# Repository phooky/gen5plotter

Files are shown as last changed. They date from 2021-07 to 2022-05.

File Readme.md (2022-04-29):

# g5plot

This software will allow you to control a generation 5 Makerbot Replicator and adapt it as a plotter.
It's adapted to my particular circumstances; ymmv. This is mostly to help myself remember when I come 
back to this project or find another junked G5.

## Initial setup

0. Disassemble the replicator until you have access to the main "birdwing" board.

1. Find the J5 connector on the birdwing board, right next to the speaker. The silkscreen will include the 
label "USB2TTL" and therevwill be an arrow pointing to Pin 1.  This is a 3.3V level serial console interface using a standard FTDI cable pinout. You can find a 3.3V FTDI USB-to-serial cable, or program an arduino or similar board with 3.3V I/O levels to act as a bridge. See the pinout section for details.

2. Open up your serial port in `tio`, `minicom`, or some other simple console. Be sure to set your baud rate to 115200. Next, turn on the PSU and push the "PowerOn" button on the birdwing board. After a few moments, you should see boot messages scrolling by. Eventually you will see a login prompt. Log in as "root"; no password should be necessary.

3. Remount the root partition as read/write: `mount -o remount,rw /`

4. Change the hostname. For convenience, I've named mine 'gen5'. If you use something else you'll need to edit the hostname in the Makefile if you want the 'deploy' and other remote targets to work. You can change the hostname by editing the `/etc/hostname` file and rebooting (or in theory running the 'hostname' utility).

5. Plug in the wired ethernet, or set up the wifi. I'm not going to document the wifi configuration here, but you can probably set it up with the 'nmcli' utility.

5. Add your public key to the /var/ssh/authorized_keys file. Run "/etc/init.d/S50sshd restart".

6. Stop the 'kaiten' process. Remove the 'kaiten' from the /etc/init.d directory (or better yet move it somewhere safe) to stop it from launching on boot. Reboot.

## Building and installing g5plot

1. Install cross-platform toolchain for ARM Linux (arm-linux-gnueabi-gcc).

2. Build PASM and the app loader libraries with the "build_tools.sh" script.

3. #`(cd g5plot && make)`

## Deploying and running

You can deploy g5plot by running `make deploy` from the g5plot directory. It relies on the hostname being `gen5`; you can either change the default in the Makefile or set the `PLOTTER` environment variable to the plotter's name.

By default g5plot is deployed to `/var/scratch/g5plot`. If you want to deploy it outside of the `/var` tree you'll need to remount the root partition as read/write.

You can use the `g5p_start.sh` and `g5p_stop.sh` scripts to start and stop the plotter process. Commands should be piped to `/var/run/plotter`.

## TODOs

* Start using the speaker for alerts

## Pinouts

### J5 UART

To connect to the birdwing board you will need to wire up GND, TX, and RX only. It's safest to leave the other pins disconnected.

| Pin | Function |
|-----|---|
|  1  | GND |
|  2  | CTS (ignore) |
|  3  | VCC (ignore) |
|  4  | TX |
|  5  | RX |
|  6  | RTS (ignore) |

### Servo hookup

TODO

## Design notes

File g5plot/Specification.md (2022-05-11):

== Overview

The plotter is controlled by the `g5plot` process, which takes simpled
commands from standard input and uses them to control the plotter. It
terminates and shuts down the plotter cleanly when it receives a SIGINT
signal. SIGSTOP/SIGTSTP and SIGCONT can be use to pause and continue
execution, but be aware that the currently queued commands will
continue to be executed if SIGSTOP is sent. SIGTSTP will immediately
halt the PRUs and reenable them on continuation.

== Interface

=== g5plot interface

Commands are seperated by newlines. All parameters are floats if not
otherwise specified.

| command code | parameters | explanation |
|---|---|---|
| U | - | toolhead up (to preset value) |
| D | - | toolhead down (to preset value) |
| M | X Y V | move toolhead. X and Y are in mm, V is in mm/sec. |
| R | X Y V | move toolhead relative to last position. X and Y are in mm, V is in mm/sec. |
| T | V | move toolhead to velue. Toolhead value is a one-byte unsigned integer. |
| Z | - | set current position as zero/home. |
| O | - | all steppers off |
| H | - | home toolhead to 0,0. |
| Q | - | shut down plotter. |
| W | - | wait for user intervention (NOT YET IMPLEMENTED) |

While g5plot can be driven directly from the command line, the
intended use is to have it receive commands from a fifo, generally
`/var/run/plotter`.

=== Plotter queue management

* dropping and launching prepared files
* modules for handling gcode and svg
* simulator

== Internals

Command queue is in PRU0 data RAM, which is 0x1ff bytes long.
A command is five 32-bit words (16 bytes): a velocity for each axis,
a total length in PRU ticks, and four bytes for axis direciton/enable
and top-level commands.

We do not use interrupts; instead we busy-wait on a ready bit in each
command. That means that to reliably perform a command, it needs to be
written twice: once without the ready bit set, and again with it set.

It's possible that this is unnecessary, as we could put the flag in 
the last byte to be written, but it's not worth the effort to find out
for a useless optimization.

=== Command Queue

The command queue is 20 commands long. The command queue
offset should is reset manually by the sender. Ordinarily it
resets it after 18 commands, but this could be changed easily.

=== Command byte

The command byte is a bitfield. Every command is a "move toolhead"
command, so if the command is only for the toolhead or is a dwell, the
[xyz]_period fields should be set to 0xffffffff.

The bits on the command flag are:

| bit | name | explanation |
|-----|---|---|
| 0 | WAIT | 'WAIT' is deprecated. |
| 1 | READY | The READY flag is set when a command is ready to be executed, and cleared by the PRU once execution has started. |
| 2 | RESET | After this command is executed, the PRU should begin reading the next command from the start of the command buffer. |
| 3 | TOOLHEAD | This command contains a toolhead payload byte which should be sent to the toolhead PRU. |

== TODO

What about acceleration?

What about zeroing?

At start of command, we have a current X Y Z

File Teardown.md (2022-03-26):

# Controlling a Gen 5 Replicator

## Introduction and motivation

A while back I was gifted a busted-up Makerbot Replicator Generation 5 (henceforth just "gen5"). It
was too mechanically damaged to serve as a printer again, but I figured I could pull out the gantry 
and use it as a pen plotter. Unfortunately the existing software on the gen5 was unsuitable for
my purposes, and I ended up having to write a new stepper driver from scratch.

## Anatomy

This is a quick breakdown of the major parts of the gen5. This is all based on my teardown, comments
in the software, and silkscreens on the PCBs; Makerbot may use other terminology.

* Birdwing - the mainboard. Carries the AM1808 processor and the X/Y/Z stepper drivers, along with
    ethernet, wifi, and a six-pin serial console connection.
* Hoboken - the interface PCB. Hoboken includes the knob and buttons, the screen, the thumbdrive USB port,
    the camera, and the chamber lighting LED. Hoboken is connected to Birdwing via an HDMI cable and standard
    connectors. The cable does not actually carry HDMI signals. The video is routed over a single
    signal pair. There is a USB hub on board that routes signals from the camera and thumbdrive.
* Bronx - the toolhead PCB. This is the PCB inside the toolhead, not the one inside the extruder. It has a
    stepper driver and probably some mosfets. It connect via a large flexible flat cable.
* PSU - a small ATX power supply
* H-bot - the XY gantry is in a so-called "h-bot" configuration, with one continuous belt.

## Getting in

### Step one: console

Find the J5 connector on the birdwing board, right next to the speaker. The silkscreen will include the 
label "USB2TTL" and there
will be an arrow pointing to Pin 1.  This is a 3.3V level serial console interface using a standard FTDI cable
pinout. You can find a 3.3V FTDI USB-to-serial cable, or program an arduino or similar board with 3.3V I/O levels
to act as a bridge.

Open up your serial port in `tio`, `minicom`, or some other simple console. Be sure to set your baud rate to 115200.
Next, turn on the PSU and push the "PowerOn" button on the birdwing board. After a few moments, you should see boot
messages scrolling by. Eventually you will see a login prompt. Log in as "root"; no password should be necessary.

### Step two: ethernet and ssh

add pub key to /var/ssh/authorized_keys 
`# /etc/init.d/S50sshd restart`

### Step three: stop kaiten

## Build instructions

build pasm
get arm tools
build entire thing

The easiest way is to use a 115200
 
I'll just refer to the Replicator as the "gen5" going forward.

## TODOs

* Where is the speaker?

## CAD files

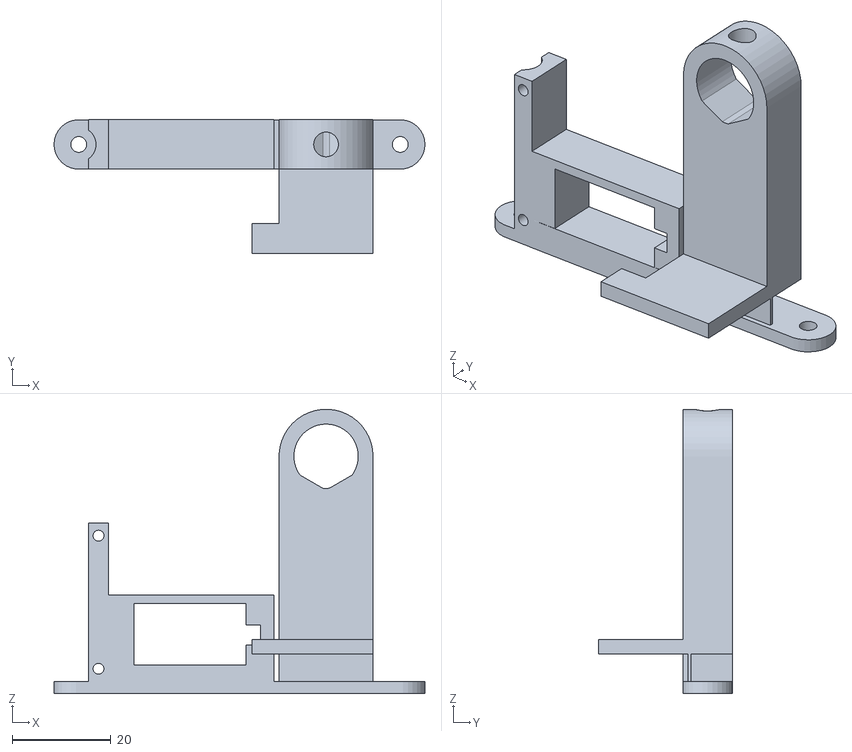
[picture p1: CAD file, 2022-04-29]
hardware/penholder.stl
75.0 x 27.0 x 57.5

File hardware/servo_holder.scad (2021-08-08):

m3_head_clearance = 5.3;
m3_screw_clearance = 3.2;
$fn=30;

module m3_bolt(bolt_len) {
    head_len=5;
    translate([0,0,bolt_len/2]) cylinder(d=m3_screw_clearance,h=bolt_len+0.05,center=true);
    translate([0,0,-head_len/2]) cylinder(d=m3_head_clearance,h=head_len,center=true);
}

module bolts(hole_distance,bolt_len) {
    translate([hole_distance/2,0,0]) m3_bolt(bolt_len);
    translate([-hole_distance/2,0,0]) m3_bolt(bolt_len);
}

// clearance between bolthole center and belt
upper_clearance = 5.0;

// measured parameters
hole_distance = 65.0;
bolt_len = 15.0;

module support(support_th) {
    difference() {
        hull() {
            translate([hole_distance/2,0,support_th/2])
                cylinder(r=upper_clearance,h=support_th,center=true);
            translate([-hole_distance/2,0,support_th/2])
                cylinder(r=upper_clearance,h=support_th,center=true);
        }
        translate([0,0,-0.05]) bolts(hole_distance, bolt_len);
    }
}

servo_screw_hole_d = 1.8;

module pillar() {
    ht_to_under_flange=16;
    difference() {
        hull() {
            translate([0,0,2.5]) cube([4.5,upper_clearance*2,5],center=true);
            translate([0,0,ht_to_under_flange-2.5]) cube([4.5,12,5],center=true);
        }
        translate([1,0,ht_to_under_flange]) cylinder(d=servo_screw_hole_d,h=16,center=true);
    }
}

module pillars() {
    translate([27.5,0,0]) pillar();
    difference() {
        mirror([1,0,0]) pillar();
        translate([0,2.7,0]) cube([10,10,12],center=true);
    }
}

support(2.5);
translate([-15,0,0]) {
color([1,0,0])
#translate([-1.5,-50-(12-upper_clearance*2)/2,16 + 2.5]) import("sg90.stl",convexity=3);
translate([0,0,2.49]) pillars();
}
//translate([0,0,2.49])
//hinge_a();
//rotate(-90,[1,0,0])
//translate([0,-2.9,0]) simple_penholder(15);

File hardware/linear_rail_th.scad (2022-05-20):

use <sg90.scad>
use <mounting.scad>

// Constants

// ----- M2 fastener -----
m2_bolt_head_dia = 3.8; // mm
m2_bolt_head_clearance_dia = 4.4; // mm
m2_bolt_head_height = 2; // mm
m2_bolt_thread_dia = 2; // mm
m2_bolt_thread_clearance_dia = 2.4; // mm
m2_bolt_length = 10; // mm

// ----- Linear rail -----
rail_width = 9; // mm
rail_height = 6.3; // mm
rail_length = 100; // mm
m2_mounting_height = 4.6; // mm
rail_first_hole_offset = 10; // mm
rail_successive_offset = 20; // mm

// ----- M2 hex nut ------
m2_hex_width = 4; // mm
m2_hex_nut_depth = 1.6; // mm (usual depth)
m2_hex_width_clearance = 4.5; // mm

// ----- Linear rail support -----
rail_support_height =  m2_bolt_length - m2_mounting_height; // mm
// support has a lip at one end to help locate the rail vertically
rail_support_lip_width = 1.5; // mm
rail_support_lip_height = 1; // mm

module m2_fastener_hole(length = 20, head_ht = 20) {
    $fn = 40;
    // The hole is located with the origin at the base of the head.
    // The fastener is oriented with the thread in the -Z direction.
    cylinder(d=m2_bolt_head_clearance_dia, h=head_ht); // bolt head
    // threaded bolt
    translate([0,0,-length])
	cylinder(d=m2_bolt_thread_clearance_dia, h=length+0.1); // 0.1 adjustment to ensure overlap
}

// mock fastener for assembly testing
module m2_fastener(length = m2_bolt_length, head_ht = 2) {
    $fn = 40;
    // The hole is located with the origin at the base of the head.
    // The fastener is oriented with the thread in the -Z direction.
    cylinder(d=m2_bolt_head_dia, h=head_ht); // bolt head
    // threaded bolt
    translate([0,0,-length])
	cylinder(d=m2_bolt_thread_dia, h=length+0.1); // 0.1 adjustment to ensure overlap
}

module rail_holes(rail_length = 100, mocks=false) {
    // located from bottom center of one end of the rail; rail extends in +Y direction
    for (offset = [rail_first_hole_offset : rail_successive_offset : rail_length]) {
	translate([0,offset,m2_mounting_height])
	    if (mocks) m2_fastener();
	    else m2_fastener_hole();
    }
}

module rail_approximate(rail_length = 100) {
    color("red") difference() {
	translate([-rail_width/2,0,0])
	    cube([rail_width,rail_length,rail_height]);
	rail_holes();
    }
}

module m2_hex_nut_hole(depth=10) {
    // located from the center of the nut, bottom face
    $fn=40;
    intersection_for(theta = [0, 60, 120]) {
	rotate([0,0,theta])
	    translate([0,0,depth/2])
	    cube([m2_hex_width_clearance,100,depth],center=true);
    }
    translate([0,0,-20])
	cylinder(d=m2_bolt_thread_clearance_dia,h=40);
}

module rail_support(rail_length = 100) {
    difference() {
	union() { // rail support + lip
	    translate([-rail_width/2,0,0])
		cube([rail_width + rail_support_lip_width,
		      rail_length,
		      rail_support_height]);
	    translate([rail_width/2,0,rail_support_height])
		cube([rail_support_lip_width,
		      rail_length,
		      rail_support_lip_height]);
	}
	// holes for hex nuts
	for (offset = [rail_first_hole_offset : rail_successive_offset : rail_length]) {
	    translate([0,offset,m2_hex_nut_depth])
		rotate([180,0,0]) m2_hex_nut_hole();

	}
    }
}

//m2_hex_nut_hole();
translate([0,0,rail_support_height]) {
    // #color("green") rail_holes(mocks=true);	
    // #rail_approximate();
}
rail_support();
support(4);

// *** copied from sg90.scad, ugh "use" vs "import" ***
m_body_width = 23;
m_body_wing_height = 2.5;
m_body_depth = 12.5;

// ----- mounting holes ----
sg90_mounting_hole_dia = 2.5; // mm
sg90_mounting_hole_d_from_body = 2.65; // mm
sg90_mounting_hole_separation = m_body_width + sg90_mounting_hole_d_from_body * 2;

module sg90_support() {
    mount_th = 5;
    mount_w = (sg90_mounting_hole_d_from_body*2) - 0.1;
    mount_d = m_body_depth;
    module one_mount() {
	// located with origin at the top of the mounting hole
	difference() {
	    translate([0,0,-mount_th/2])
		cube([mount_w,mount_d,mount_th], center=true);
	    translate([0,0,-mount_th + m2_hex_nut_depth])
		rotate([180,0,0]) m2_hex_nut_hole();
	}
    }
    one_mount();
    translate([sg90_mounting_hole_separation,0,0]) one_mount();
}

sg90_support_height = 10 - m_body_wing_height;
translate([18,30,sg90_support_height]) {
    rotate([0,0,90]) {
	//# sg90_mount_origin();
	sg90_support();
    }
}
// bridge. this is hacky but whatevs, i'm busy
color("orange")
hull() {
    translate([18-m_body_depth/2,27.3,sg90_support_height-5])
	cube([0.05,5.6+sg90_mounting_hole_separation,5]);
    translate([rail_width/2,28,rail_height-5])
	cube([0.05,4+sg90_mounting_hole_separation,5]);
}

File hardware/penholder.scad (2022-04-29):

use <sg90.scad>
use <mounting.scad>

filament_diameter = 1.75 + 0.15;
clip_diameter = 5;
clip_ht = 3.5;

guide_width = 25;
guide_th = 2;

$fn=45;
thumbscrew_bolt_diameter = 5;

clearances_motor = 0.1;
module motor_bracket() {
    cm = clearances_motor;
    difference() {
        translate([-10,0,10])
        cube([34,10,20], center=true);
        translate([-10,18 - (5 + 2.5),12])
        rotate([90,0,0])
        union() {
            minkowski() {
                sg90(horn_angle=30);
                cube([cm,cm,cm], center=true);
            }
            // cable entry clearance
            hull() {
                translate([-0.5,0,12])
                cord(length=3);
                cord(length=4);
            }
        }
    }
}

module pen_holder() {
    ph_h = 10;
    outer_diameter = 19;
    inner_diameter = 13;
    center_to_hinge = 40;
    translate([-outer_diameter/2,0,0])
    cube([outer_diameter,3,27]);
    translate([-15,0,27-6])
    cube([10,3,6]);
    difference() { 
        hull() { // outside of holder
            translate([0,center_to_hinge,0])
            cylinder(h=ph_h,d=outer_diameter);
            translate([-outer_diameter/2,0,0])
            cube([outer_diameter,1,ph_h]);
        }
        translate([0,center_to_hinge,0])
        intersection() {
            cylinder(h=22,d=inner_diameter,center=true);
            translate([0,4.7,0])
            intersection_for( i = [30,-30] ) {
            rotate([0,0,i])
            cube([20,20,22],center=true);
            }
        }
        translate([0,center_to_hinge,ph_h/2])
        rotate([-90,0,0])
        cylinder(d=5, h=20);
    }
}

module pen_hinge() {
    translate([8,-4,0])
    cube([19,0.7,15]);
    translate([8+19/2,5,8])
    rotate([90,0,0])
    pen_holder();
}



gl_ht = 10.0;
gl_width = 32.0;
gl_depth = 4.0;

module guide () {
    difference(){
    translate([-28.5,0,2.5+gl_width/2])
    rotate([0,90,0])
    rotate([90,0,0])
    difference() {
        // body
        cube([gl_width,gl_depth,gl_ht],center=true);
        // filament holes
        for (theta = [90, -90]) {
            rotate([0,0,theta])
            translate([0,(guide_width+filament_diameter)/2,0])
            cylinder(d=filament_diameter+0.3, h=100,center=true);
        }
    }
    translate([-65/2,0,0])
    cylinder(d=7,h=40);
    }
}

//#color("#8080ff") 
//translate([-10,18 - (5 + 2.5),12])
//rotate([90,0,0]) sg90(horn_angle=0);
union() {
    support(2.5);
    motor_bracket();
    guide();
}
color("#00ff00") pen_hinge();

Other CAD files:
hardware/mounting.scad
hardware/sg90.scad
hardware/tap_holder.scad

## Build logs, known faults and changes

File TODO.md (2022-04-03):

* TODO Proper check for whether a command has been executed; we need a bit to indicate that this command has not yet been handled. This will allow us to have proper pipeline stalls, instead of the mess I'm currently grappling with.

* TODO simplify servo PRU design; it should simply run continuously instead of awaiting a signal (with the possible ability to go into "servo off" mode where no pulses are sent)

* DONE QUICK NOTES: not exiting correctly-- hangs on cherchar(), but also wait  for completion. Let's review
  CLOSED: [2022-03-31 Thu 20:01]

* [DONE] find penup/pendown solenoid breakout (gowanus connector?)
* look into homing
* [DONE] check gpio pins:
	DA850_GPIO5_5,	//Chamber heater reserved 0
	DA850_GPIO2_5,	//Chamber heater reserved 1
* [DONE] test basic GPIO toggling from PRU1
* DONE servo test from PRU1
  CLOSED: [2022-03-30 Wed 11:27]
* DONE pru0->pru1 servo command
  CLOSED: [2022-03-30 Wed 11:27]

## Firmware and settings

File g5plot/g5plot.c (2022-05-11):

#include <stdio.h>
#include <stdint.h>
#include <string.h>
#include <stdlib.h>
#include <math.h>
#include <stdbool.h>

// PRU driver headers
#include <prussdrv.h>

#define STEPPER_PRU     0
#define TOOLHEAD_PRU    1

// Command structure that is sent to the PRU.
typedef struct {
    uint32_t x_period;
    uint32_t y_period;
    uint32_t z_period;
    uint32_t end_tick;
    uint8_t direction;
    uint8_t enable;
    uint8_t cmd;
    uint8_t toolhead;
} __attribute__((packed,aligned(4))) Command;

const unsigned int CommandSzInWords = 5;

const unsigned int TH_UP = 30;
const unsigned int TH_DOWN = 200;

// Command byte bit definitions
enum {
    CFL_WAIT = 0,        // Deprecated
    CFL_CMD_READY = 1,   // Indicates that this command is ready for processing.
                         // If this bit is not set, the PRU will busy wait until it is.
    CFL_RST_QUEUE = 2,   // Indicates that after this command is executed, the PRU should go
                         // back to the head of the buffer.
    CFL_TOOLHEAD = 3,    // Indicates that this command is for the toolhead.
};

// A running count of commands processed since g5plot was started.
uint16_t cmds_processed = 0;

// A pointer to the PRU0's data memory, used for command queue management.
uint8_t* prumem = NULL;

// Flag indicating that g5plot is ready to shut down.
static volatile bool shutdown = false;

// Queue management
uint8_t queue_idx = 0; // next empty queue slot
const uint8_t queue_len = 20; // total number of Command entries in queue

// Check if we're running or not
bool is_running = false;

void enqueue(Command* cmd) {
    int byteoff = queue_idx * sizeof(Command);
    volatile Command* prucmd = (Command*)(prumem + byteoff);
    // clear reset flag and ready flag on existing command, just in case
    cmd->cmd &= ~((1 << CFL_RST_QUEUE) | (1 << CFL_CMD_READY));
    // zero the queue after this entry if near the end
    bool zero_queue = (queue_idx >= queue_len - 2);
    if (zero_queue) {
        cmd->cmd |= 1 << CFL_RST_QUEUE;
    }
    // wait for empty command space
    printf("Checking for space at queue entry %d (of %d).\n",
	   queue_idx, queue_len); fflush(stdout);
    if (prucmd->cmd & (1<<CFL_CMD_READY)) {
	uint32_t attempts = 0;
	while ((prucmd->cmd & (1<<CFL_CMD_READY)) && !shutdown) {
	    // pass and busy wait, we should check for timeouts at some point
	    if (attempts == 0xffff) { printf("Busy waiting"); fflush(stdout); }
	    attempts++;
	}
	printf("Block cleared.\n"); fflush(stdout);
    }
    *prucmd = *cmd;
    // Set ready bit
    cmd->cmd |= 1 << CFL_CMD_READY;
    *prucmd = *cmd;
    queue_idx = zero_queue?0:queue_idx+1;
}


/*
 * Machine configuration
 */
const float steps_per_mm = 100.0;
// Maximum X coordinate in millimeters
const float max_x = 252.0;
// Maximum Y coordinate in millimeters
const float max_y = 199.0;
// Maximum velocity in mm/s
const float max_v = 150.0;
// Steps per mm, XY
const float steps_per_mm_xy = 88.573186;
// Steps per mm, Z
const float steps_per_mm_z = 400.0;
// Internal PRU ticks per second (200 MHz)
const float ticks_per_second = 200 * 1000 * 1000;

// Toolhead ticks: needs 0.2s
const uint32_t TH_TICKS = 40L * 1000L * 1000L;

// Homing ticks: needs 5s
const uint32_t HOMING_TICKS = 1000L * 1000L * 1000L;


/*
 * Machine state
 */
// The _machine_ state is maintained as the current position in A and B
// steps. The XY coordinates are always a cache of the XY interpretation
// of the A and B steps.
typedef struct { int32_t a; int32_t b; } AB;
typedef struct { float_t x; float_t y; } XY;
struct {
    AB ab;    // Absolute stepper positions
    XY xy;    // xy coordinates based on ab coordinates
} state = { { 0, 0 }, { 0.0, 0.0 } };

/** Convert XY position or delta to AB position or delta */
AB ab_from_xy(XY xy) {
    int32_t steps_x = (int32_t)(xy.x * steps_per_mm_xy);
    int32_t steps_y = (int32_t)(xy.y * steps_per_mm_xy);
    return (AB){ steps_y + steps_x, steps_y - steps_x };
}

/** Convert AB position or delta to XY position or delta */
XY xy_from_ab(AB ab) {
    int32_t steps_x = (ab.a - ab.b) / 2;
    int32_t steps_y = (ab.a + ab.b) / 2;
    return (XY){ (float)steps_x / steps_per_mm_xy, (float)steps_y / steps_per_mm_xy };
}

/*
 * Enqueue a relative AB move, in steps and timer ticks
 */
void move_rel_ab_time(AB ab, uint32_t ticks) {
    Command cmd;
    cmd.end_tick = ticks;
    cmd.enable = 0x4;
    cmd.direction = 0x1;
    int32_t a = ab.a; int32_t b = ab.b;
    if (a < 0) { cmd.direction ^= 0x1; a = -a; }
    if (b < 0) { cmd.direction ^= 0x2; b = -b; }
    cmd.cmd = 0x00;
    cmd.z_period = ticks + 1;
    //printf("X %d Y %d A %d B %d\n",x_delta,y_delta,a,b);
    cmd.x_period = (a==0)?0x7fffffff:(ticks / (a * 2));
    cmd.y_period = (b==0)?0x7fffffff:(ticks / (b * 2));
    //printf("X_P %d Y_P %d\n",cmd.x_period, cmd.y_period);
    enqueue(&cmd);
    // Update the current machine state
    state.ab.a += ab.a;
    state.ab.b += ab.b;
    state.xy = xy_from_ab(state.ab);
}

/*
 * Home toolhead. This involves just spinning the A axis and disabling the B
 * axis.
 */
void home_toolhead() {
    Command cmd;
    cmd.end_tick = HOMING_TICKS;
    cmd.enable = 0x6;
    cmd.direction = 0x0;
    cmd.cmd = 0x00;
    cmd.y_period = cmd.z_period = 0x7fffffff;
    cmd.x_period = HOMING_TICKS / (max_x * steps_per_mm_xy * 2);
    enqueue(&cmd);
}


/*
 * Disable steppers.
 */
void disable_steppers() {
    Command cmd;
    cmd.end_tick = TH_TICKS;
    cmd.enable = 0x7;
    cmd.direction = 0x0;
    cmd.cmd = 0x00;
    cmd.x_period = cmd.y_period = cmd.z_period = 0x7fffffff;
    enqueue(&cmd);
}

/**
 * Move in XY coordinates relative to the current position.
 * Ignores commands that try to move at exceptionally low speeds.
 * TODO: check for overlong moves (max: 10s)
 * @param dx the delta x coordinate in millimeters (mm).
 * @param dy the delta y coordinate in millimeters (mm).
 * @param v the velocity of the move, in millimeters per second (mm/s).
 */
void move_relative_xy(float dx, float dy, float v) {
    if (fabsf(v) <= 0.1) {
        fprintf(stderr, "Refusing to move at less that 0.1mm/s\n");
        return;
    }
    AB delta = ab_from_xy( (XY){ dx, dy } );
    float len = sqrt(dx*dx + dy*dy);
    uint32_t time_in_ticks = (uint32_t)(ticks_per_second * (len / v));
    move_rel_ab_time(delta,time_in_ticks);
}

/**
 * Move to the specified XY coordinates from current position.
 * @param x the x coordinate in millimeters (mm).
 * @param y the y coordinate in millimeters (mm).
 * @param v the velocity of the move, in millimeters per second (mm/s).
 */
void move_xy(float x, float y, float v) {
    float dx = x - state.xy.x;
    float dy = y - state.xy.y;
    move_relative_xy(dx, dy, v);
}

/**
 * Dwell at given location for a specified time.
 * TODO: check for overlong dwells (max: 10s)
 * @param t the time to dwell, in seconds
 */
void dwell(float time) {
    uint32_t time_in_ticks = (uint32_t)(ticks_per_second * time);
    move_rel_ab_time((AB){0,0},time_in_ticks);
}

void toolhead(int parameter) {
    Command cmd;
    cmd.cmd = 1 << CFL_TOOLHEAD;
    cmd.toolhead = parameter & 0xff;
    cmd.end_tick = TH_TICKS;
    cmd.enable = 0x4;
    cmd.direction = 0x1;
    cmd.z_period = 0x7fffffff;
    cmd.x_period = 0x7fffffff;
    cmd.y_period = 0x7fffffff;
    enqueue(&cmd);
}


/**
 * Set bot's idea of home (0,0).
 */
void set_here_as_home() {
    state.ab = (AB){ 0, 0 };
    state.xy = (XY){ 0.0, 0.0 };
}

/**
 * Enqueue a stop command.
 */
void stop() {
    Command cmd;
    cmd.enable = 0x0;
    cmd.cmd = 1 << CFL_WAIT;
    cmd.end_tick = 200;
    enqueue(&cmd);
}

#include <signal.h>

// Handle SIGINT by setting the shutdown flag.
void handle_sigint(int sig) {
    shutdown = true;
    printf("Interrupted; shutting down.\n");
}

static struct sigaction orig_tstp;

void handle_sigtstp(int sig) {
    prussdrv_pru_pause(0);
    (*orig_tstp.sa_handler)(sig);
}

static struct sigaction orig_cont;

void handle_sigcont(int sig) {
    prussdrv_pru_unpause(0);
    (*orig_cont.sa_handler)(sig);
}

int main(int argc, char** argv) {
    //tpruss_intc_initdata pruss_intc_initdata = interrupt_controller_setup;
    prussdrv_init();	
    if (prussdrv_open(PRU_EVTOUT_0)) { 
        fprintf(stderr, "Could not open uio%d, aborting\n", PRU_EVTOUT_0);
        return -1;
    }
    fprintf(stderr,"Opened PRU.\n");
    
    // Initialize interrupts
    //prussdrv_pruintc_init(&pruss_intc_initdata);

    if (prussdrv_map_prumem(PRUSS0_PRU0_DATARAM, (void**) &prumem) != 0) {
	fprintf(stderr, "Could not map PRU0 data ram! Aborting.\n");
	return -1;
    }
    
    // Clear out command buffer to ensure no accidental commands are run
    {
	const int wordsz = sizeof(Command)*queue_len / 4;
	for (int i = 0; i < wordsz; i++) {
	    *((uint32_t*)prumem + i) = 0;
	}
    }

    // Run PRU programs
    prussdrv_exec_program(TOOLHEAD_PRU, "./servo_pru.bin");
    prussdrv_exec_program(STEPPER_PRU, "./stepper_pru.bin");

    {
	struct sigaction sa_int = { .sa_handler = handle_sigint, .sa_flags = 0 };
	sigaction(SIGINT, &sa_int, NULL);
	struct sigaction sa_tstp = { .sa_handler = handle_sigtstp, .sa_flags = 0 };
	sigaction(SIGTSTP, &sa_tstp, &orig_tstp);
	struct sigaction sa_cont = { .sa_handler = handle_sigcont, .sa_flags = 0 };
	sigaction(SIGCONT, &sa_cont, &orig_cont);
    }

    int cmd;

    while (!shutdown) {
	cmd = getchar();
	if (cmd == EOF) {
	    clearerr(stdin);
	    continue;
	}
	if (cmd == 'U') {
	    printf("Pen up\n");
	    toolhead(TH_UP);
	}
	if (cmd == 'D') {
	    printf("Pen down\n");
	    toolhead(TH_DOWN);
	}
	if (cmd == 'H') {
	    printf("Homing.\n");
	    home_toolhead();
	}
	if (cmd == 'O') {
	    printf("Steppers off.\n");
	    disable_steppers();
	}
	if (cmd == 'Z') {
	    printf("Now at 0,0\n");
	    set_here_as_home();
	}
	if (cmd == 'Q') {
	    printf("Explicit shutdown.\n");
	    shutdown = true;
	}
        if (cmd == 'M') {
            float x_in, y_in, v_in;
            if (scanf("%f %f %f\n",&x_in,&y_in,&v_in) != EOF) {
                move_xy(x_in,y_in,v_in);
                printf("Move to X %f Y %f - V %f\n",x_in,y_in,v_in);
            }
	}
        if (cmd == 'R') {
            float x_in, y_in, v_in;
            if (scanf("%f %f %f\n",&x_in,&y_in,&v_in) != EOF) {
                move_relative_xy(x_in,y_in,v_in);
                printf("Move relative X %f Y %f - V %f\n",x_in,y_in,v_in);
            }
	}
        if (cmd == 'T') {
            int th;
            if (scanf("%d\n",&th) != EOF) {
                toolhead(th);
                printf("Sending %d to toolhead\n",th);
            }
        }
    }

    printf("Out of main loop.\n");

    printf("SUMMARY: oustanding events %d, processed events %d, queue offset %d\n",
	   0, cmds_processed, queue_idx);

    prussdrv_pru_disable(STEPPER_PRU);
    prussdrv_pru_disable(TOOLHEAD_PRU);
    prussdrv_exit ();

    return 0;
}

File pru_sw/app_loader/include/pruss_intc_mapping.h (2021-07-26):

/*
 * pruss_intc_mapping.h
 *
 * Example PRUSS INTC mapping for the application
 *
 * Copyright (C) 2010 Texas Instruments Incorporated - http://www.ti.com/
 *
 *
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
 *    Redistributions of source code must retain the above copyright
 *    notice, this list of conditions and the following disclaimer.
 *
 *    Redistributions in binary form must reproduce the above copyright
 *    notice, this list of conditions and the following disclaimer in the
 *    documentation and/or other materials provided with the
 *    distribution.
 *
 *    Neither the name of Texas Instruments Incorporated nor the names of
 *    its contributors may be used to endorse or promote products derived
 *    from this software without specific prior written permission.
 *
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
*/

/*
 * ============================================================================
 * Copyright (c) Texas Instruments Inc 2010-11
 *
 * Use of this software is controlled by the terms and conditions found in the
 * license agreement under which this software has been supplied or provided.
 * ============================================================================
*/

#ifdef AM33XX
#error ONLY_AM18xx
#define PRU0_PRU1_INTERRUPT     17
#define PRU1_PRU0_INTERRUPT     18
#define PRU0_ARM_INTERRUPT      19
#define PRU1_ARM_INTERRUPT      20
#define ARM_PRU0_INTERRUPT      21
#define ARM_PRU1_INTERRUPT      22
#else
#define PRU0_PRU1_INTERRUPT     32
#define PRU1_PRU0_INTERRUPT     33
#define PRU0_ARM_INTERRUPT      34
#define PRU1_ARM_INTERRUPT      35
#define ARM_PRU0_INTERRUPT      36
#define ARM_PRU1_INTERRUPT      37
#endif
#define CHANNEL0                0
#define CHANNEL1                1
#define CHANNEL2                2
#define CHANNEL3                3
#define CHANNEL4                4
#define CHANNEL5                5
#define CHANNEL6                6
#define CHANNEL7                7
#define CHANNEL8                8
#define CHANNEL9                9

#define PRU0                    0
#define PRU1                    1
#define PRU_EVTOUT0             2
#define PRU_EVTOUT1             3
#define PRU_EVTOUT2             4
#define PRU_EVTOUT3             5
#define PRU_EVTOUT4             6
#define PRU_EVTOUT5             7
#define PRU_EVTOUT6             8
#define PRU_EVTOUT7             9

#define PRU0_HOSTEN_MASK            0x0001
#define PRU1_HOSTEN_MASK            0x0002
#define PRU_EVTOUT0_HOSTEN_MASK     0x0004
#define PRU_EVTOUT1_HOSTEN_MASK     0x0008
#define PRU_EVTOUT2_HOSTEN_MASK     0x0010
#define PRU_EVTOUT3_HOSTEN_MASK     0x0020
#define PRU_EVTOUT4_HOSTEN_MASK     0x0040
#define PRU_EVTOUT5_HOSTEN_MASK     0x0080
#define PRU_EVTOUT6_HOSTEN_MASK     0x0100
#define PRU_EVTOUT7_HOSTEN_MASK     0x0200


#define PRUSS_INTC_INITDATA {   \
{ PRU0_PRU1_INTERRUPT, PRU1_PRU0_INTERRUPT, PRU0_ARM_INTERRUPT, PRU1_ARM_INTERRUPT, ARM_PRU0_INTERRUPT, ARM_PRU1_INTERRUPT,  (char)-1  },  \
{ {PRU0_PRU1_INTERRUPT,CHANNEL1}, {PRU1_PRU0_INTERRUPT, CHANNEL0}, {PRU0_ARM_INTERRUPT,CHANNEL2}, {PRU1_ARM_INTERRUPT, CHANNEL3}, {ARM_PRU0_INTERRUPT, CHANNEL0}, {ARM_PRU1_INTERRUPT, CHANNEL1},  {-1,-1}},  \
 {  {CHANNEL0,PRU0}, {CHANNEL1, PRU1}, {CHANNEL2, PRU_EVTOUT0}, {CHANNEL3, PRU_EVTOUT1}, {-1,-1} },  \
 (PRU0_HOSTEN_MASK | PRU1_HOSTEN_MASK | PRU_EVTOUT0_HOSTEN_MASK | PRU_EVTOUT1_HOSTEN_MASK) /*Enable PRU0, PRU1, PRU_EVTOUT0 */ \
} \

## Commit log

2021-07-07 initial checking of basic stepper engine
2021-07-21 It looks like resetting the cycle counter is... not an actual thing we can do. Looking into using a timer peripheral.
    [stepper_pru.c]
2021-07-23 adding prussdrv library to repo; we're probably going to have to horse around with it to get interrupt stuff working correctly
    [pruss_intc_mapping.h, prussdrv.c]
2021-07-26 switching over to lightly modified version of prussdrv used on the beaglebone, to fix up the mess that is INTC handling
    [pasm.h]
2021-07-27 doing some squares. Problems: - we are skipping the last move in the queue before reset - somehow not getting enough interrupts
    [stepper_pru.c]
2021-07-27 fixing reset queue bit, reducing full queue size
    [stepper_pru.c]
2021-07-28 - fixed too-small offset register size - adding wait-for-start interrupt
    [stepper_pru.c]
2021-07-28 adding commented interface, cleanup, fixing spelling, etc
    [stepper_pru.c]
2021-08-03 initial checkin of toolholder
    [pen_holder.scad]
2021-08-03 starting in on hinge design
    [pen_holder.scad]
2021-08-04 adding a hopefully useful tap handle
    [tap_holder.scad]
2021-08-08 adding another version
    [modular_pen_holder.stl]
2021-08-08 adding servo holder, quick try
    [servo_holder.scad]
2021-08-12 writing PRU code for toggling GPIO manually; this will grow into our servo code
2021-08-13 fixed servo.p PRU address, loading servo code at start
    [stepper_pru.c]
2021-08-16 switch over to verbose setup
2021-08-17 attempt to add cross-PRU interrupt
2021-08-17 changing protocol slightly to support tool commands; now sends interrupt to PRU1
2021-08-17 generate actual servo pulse
2021-08-17 send toolhead data
2022-03-26 fixing up docs, this is the programmer equivalent of puttering around your house with a screwdriver claiming you're "fixing something"
2022-03-31 first attempt at ready bit / pipeline stall
    [g5plot.c]
2022-03-31 trying to piece together new flow
2022-03-31 sigaction() instead of signal() should interrupt getchar() when necessary
2022-04-03 removing interrupt checking for toolhead; we're just going to busy poll. Still need to update on the other side
2022-04-04 Going all in on removing interrupts
2022-04-06 cleaning up, considering killing reset bit nonsense
    [g5plot.c]
2022-04-06 simplified servo, magically fixed stuff
    [g5plot.c]
2022-04-06 proper interrupts on full buffer, something's breaking somewhere, probably in PRU code
2022-04-25 missing signal parameter name
    [g5plot.c]
2022-04-25 turning on all servos for now-- not sure what I did to change the usage?
2022-04-28 added additional test script; reverted silly change due to hardware fix
    [g5plot.c]
2022-04-28 adding recent version of penholder
    [penholder.scad, penholder.stl]
2022-04-29 cleaning up some old designs
    [modular_pen_holder.stl, pen_holder.scad]
2022-04-29 adding missing servo file
    [sg90.scad]
2022-04-29 missing mounting
    [mounting.scad]
2022-05-04 fix bracket issue introduced in prior checkins
    [g5plot.c]
2022-05-04 move to new model, see if we can fix our missing step problems
    [g5plot.c]
2022-05-11 adding homing and stepper off commands
2022-05-20 adding linear rail based toolhead
    [linear_rail_th.scad]
2022-05-20 added alternate sg90 centering hacked together linear rail toolhead
    [linear_rail_th.scad, sg90.scad]
